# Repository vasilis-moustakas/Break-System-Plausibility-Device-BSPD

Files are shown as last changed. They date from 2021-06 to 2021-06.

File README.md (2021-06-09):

# Break System Plausibility Device (BSPD)
## Project Report
* Project Report is [Here](https://github.com/vasilis-moustakas/Break-System-Plausibility-Device-BSPD/blob/main/Brake_System_Plausibility_Device.pdf)
## Circuit Preview

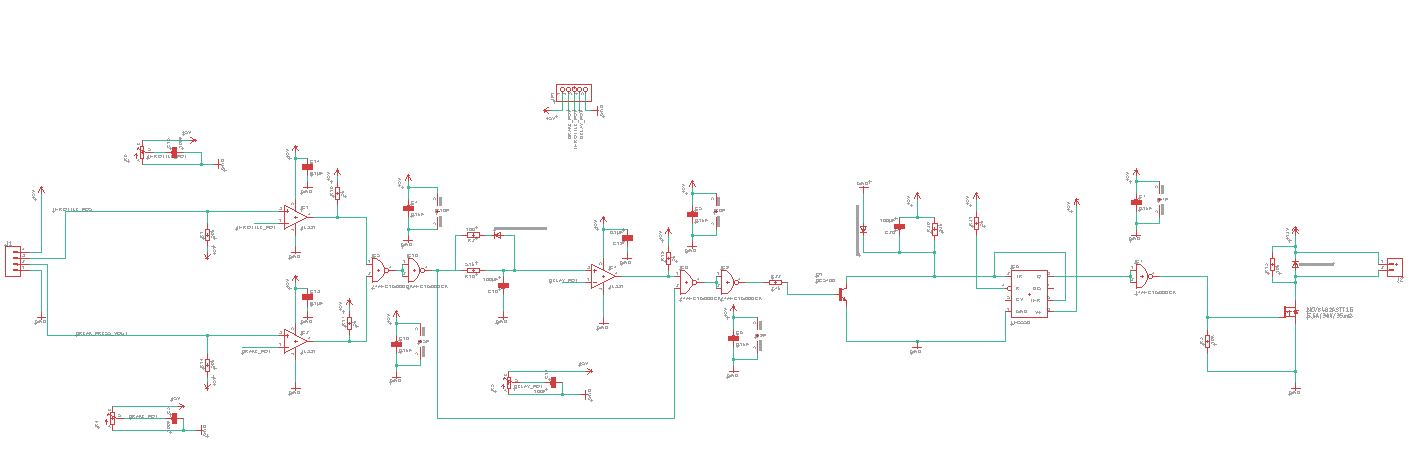
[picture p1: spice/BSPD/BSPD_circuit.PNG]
Circuit Preview


## PCB Preview
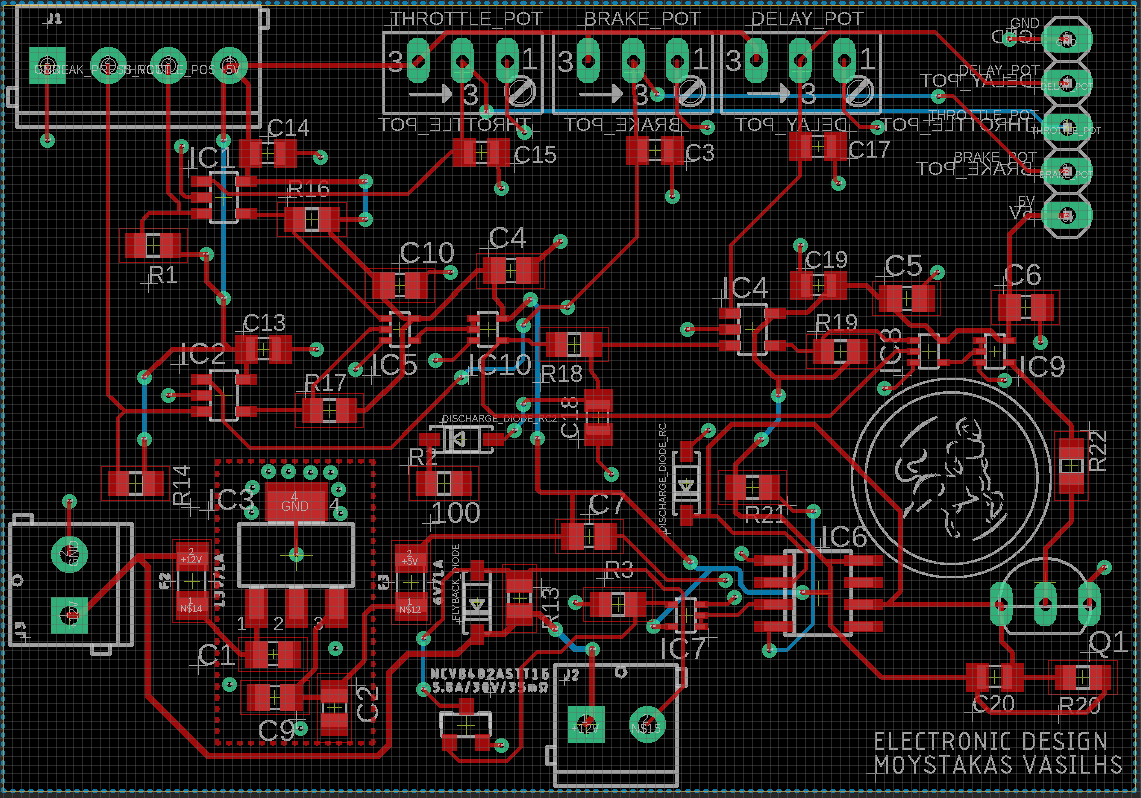
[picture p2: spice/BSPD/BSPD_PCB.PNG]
PCB Preview


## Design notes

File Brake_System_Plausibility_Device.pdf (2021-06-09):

# Brake System Plausibility Device

Vasileios Moustakas

February 2021

## 1 Introduction

With electronic throttle control systems becoming mandatory for FSAE competitions so are BSPDs . Brake System Plausibility Device (BSPD) is a standalone non-programmable circuit, witch must stop the current provision when hard braking occurs and the throttle position is more than 25 percent over the idle position for more than 500ms . Furthermore throttle and brake sensors must be able to be disconnected separately .

## 2 Regulator

As a circuit BSPD works with a 5 volts VDD but the cars battery provides 12 volts in order to reduce the voltage an LM340MP regulator was selected with 3 decoupling capacitors as shown in Fig. 1. Because the car battery is positioned away from the PCB, in case of a momentary high load there is a chance of a voltage drop due to the wiring. In that case the input capacitor of the regulator C1 provides the circuit the mandatory load for a small period of time. The regulators output capacitor improve stability, the time response of the regulator and filter part of the noise of the bandwidth. The values of the capacitors were selected according to the data sheet.

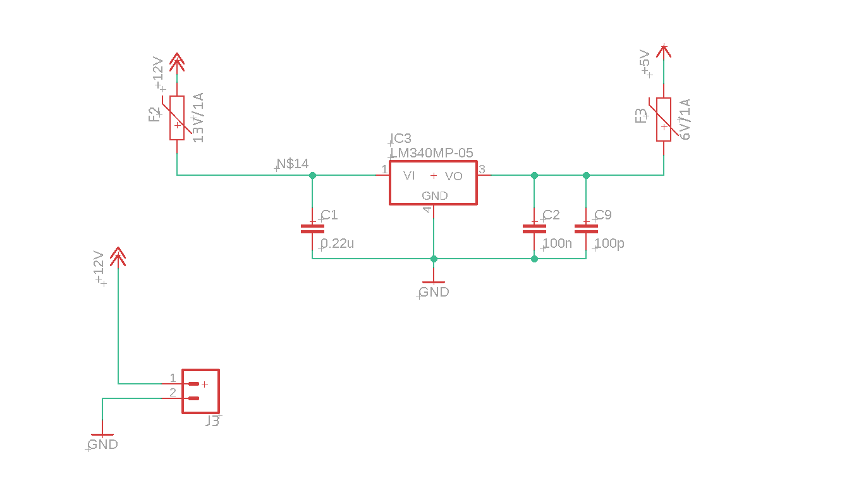
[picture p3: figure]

Figure 1: Regulator circuit

1

## 3 Comparisons and Implausibility Verification

In order to disconnect the sensor separately at any given time they must not be in the PCB and they are connected with it with a pin connector. In both sensor signal a 50K pull down resistance is connected thus when disconnecting the sensors the input signal will not be floating . The value of those resistances must be much higher of the sensor resistance in order not to interfere with the input signal. The signal from both sensor passes through an operational amplifier comparing the signals voltage with a threshold set by the user via a potentiometer in order do detect hard breaking and the throttle position. When the signal voltage is higher than the threshold op-amp is triggered providing 5 volts at the output. A 5K ohm pull up resistor is placed on output in case of an op-amp failure to provide 5V output. Both signals are connected with 2 nand gates (making an AND gate) to pass a high signal only if both throttle and brake signal are high. As set by the rules in order to trigger shut down both signal must be high for more than 500ms as such an rc filter with values 100uf for the capacitor and 5.1k(5.1 because nand gates are not ideal and the output wont be exactly 5 volts) for the resistor accompanied by an op-amp are connected with the set of nand gates . The rc filter has a time constant of 510ms given the equation for the capacitor’s charging :

Vc = Vin − (V ∗ exp (−t/(R ∗ C))) | (1)

we get an estimated 3.15 volts for the potentiometer on the other terminal of the op-amp. Finally if an implausibility happens for less than 500ms a diode is placed in order to discharge the capacitor. The capacitor is discharged to 0.7 through the diode and the 100ohm resistor and from 0.7 to 0 through the 5.1 kohm resistor. We can see all this in Fig .2

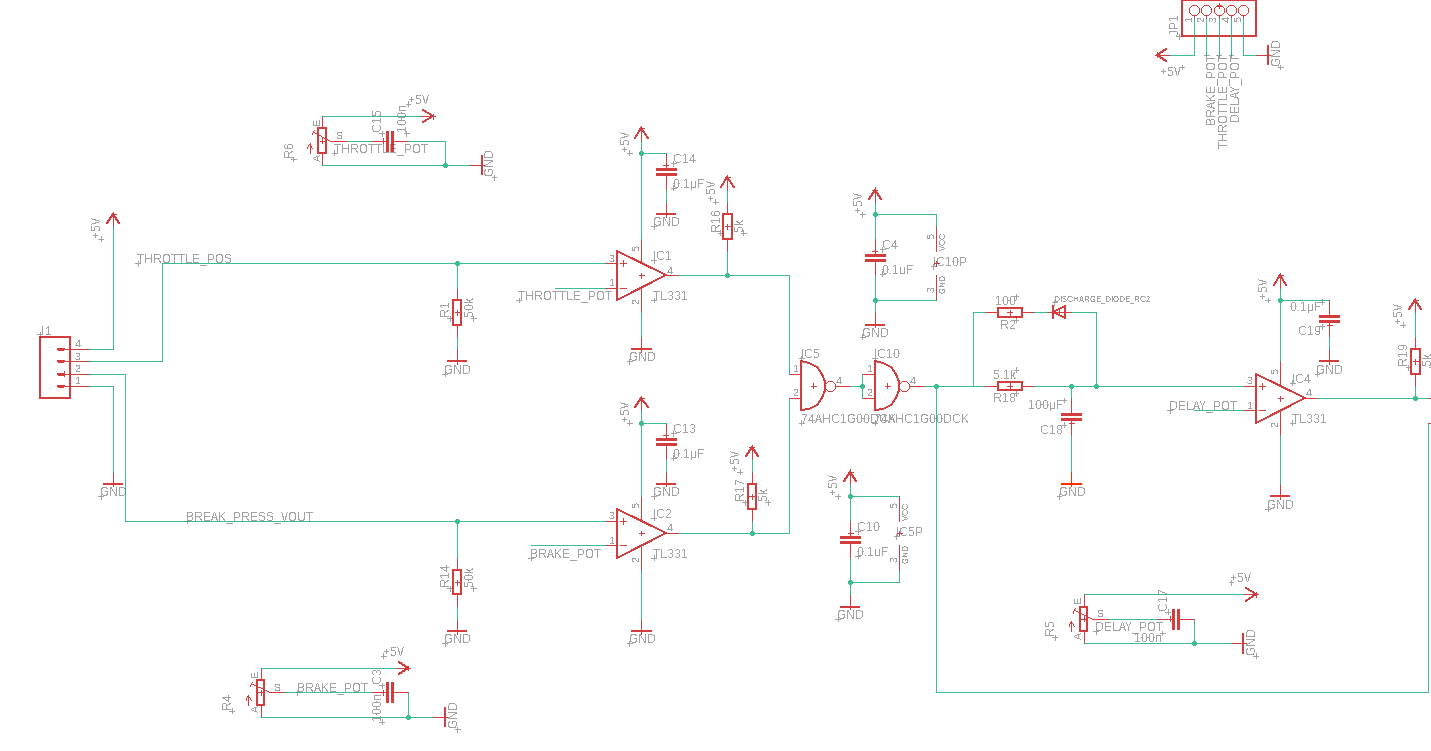
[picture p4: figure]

Figure 2: 1st part of the circuit

2

## 4 Reset Mechanisms

In order to understand the reset mechanisms first comprehend the working principle of the lm555. As shown in Fig .3 both trigger and threshold are sorted and the capacitor is connected directly to 5V so when the car powers up the capacitor instantly goes to 5V in order to avoid any false triggers. So when no implausibilities are present the bjt is open and the trigger threshold node is an open circuit, as a result its has a voltage of 5V . When VDD is present in both trigger and threshold the SR flip flop inside the lm555 goes high but the output driver inside the lm555 takes it back down to 0 so in order for the circuit to work correctly an inverter is placed on the output of the lm555. As we saw in the previous chapter when an implausibility is present for more than 500ms the bjt closes driving the trigger threshold node to GND thus the lm555 is now generating 0volts and the inverter drives it to 5volts. As stated by the rules the reset must trigger when the implausibility is aspsent for more than 10 seconds or when there is a power cycle. As for the power cycle rule when the car’s power is shut down the capacitor is immediately discharged by the diode thus reseting the lm555 output back to 0 volts. As for the 10 second rule the voltage on the trigger threshold node must reached 2/3 VDD in order to change the lm555 state thus a 100uF capacitor and a 92 kohm resistor were selected making for a timing constant of 9.2 seconds and 10 second delay for the capacitor to reach 2/3 VDD, using the equation: (1)

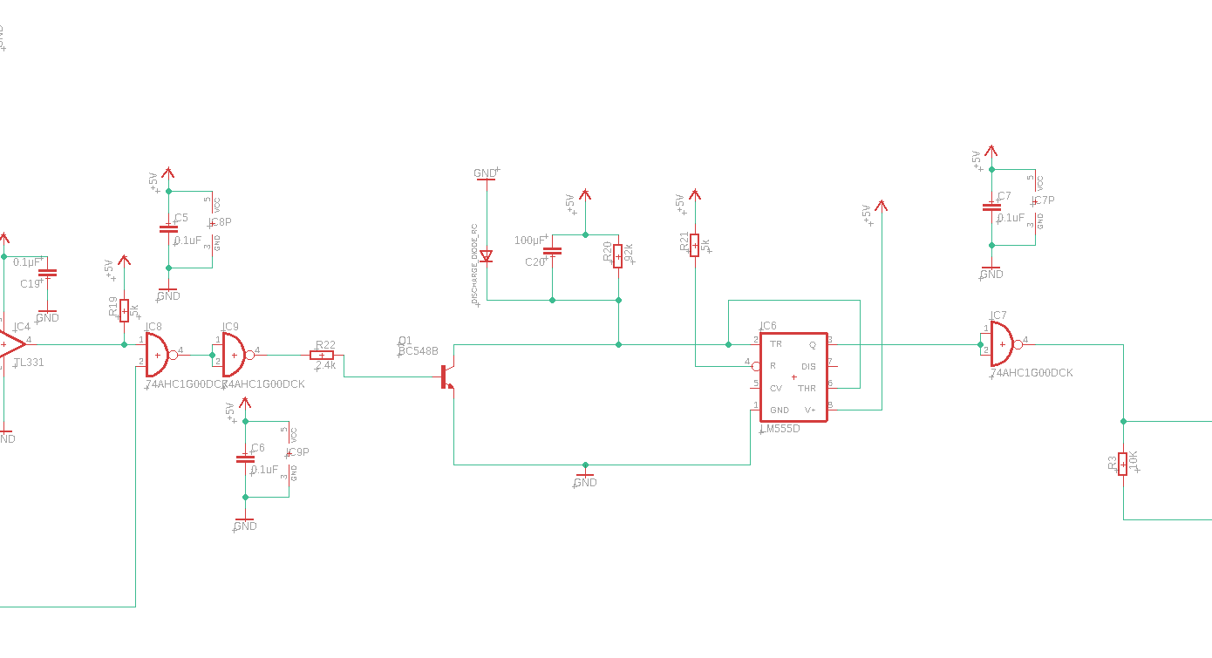
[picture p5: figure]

Figure 3: 2nd part of the circuit

3

## 5 Relay Trigeer

Finally when an implausibility is present the output of the the inverter is high thus closing the MOSFET and dragging the one terminal of the relay to 0 volts . As a results the voltage difference between the 2 terminals of the relay is 12 Volts triggering the shut down. When no implausibility is present both terminals stands at 12 volts thus not triggering the relay. Furthermore a flyback diode is placed in orded to avoid any spices due to the triggering of the coil inside the relay and a 10k pull down resistor is placed between the gate opf the MOSFET and the ground insuring that the gate can be discharged through that resistor as shown in Fig .3.

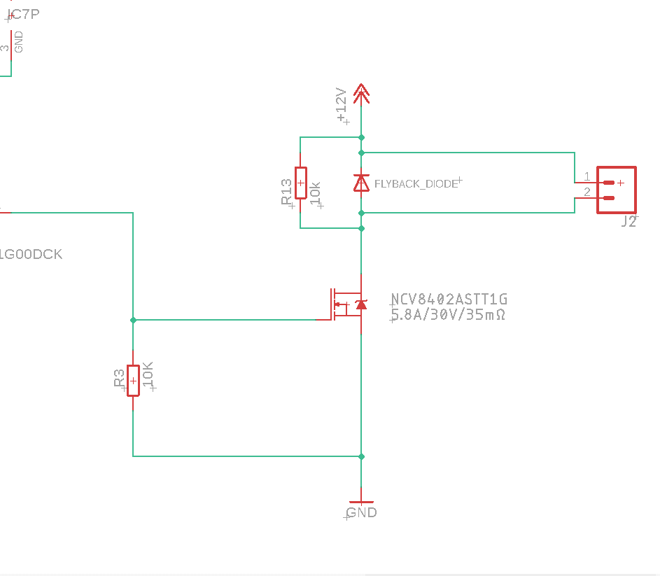
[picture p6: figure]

Figure 4: 3rd part of the circuit

4

## 6 Full circuit


Figure 5: Full circuit

## 7 Simulation results

The proposed circuit was designed using autodesk EAGLE and simulated with ltspice . As shown in Fig .6 when the implausbility lasts for 500ms or less there is no trigger of the relay and the capacitor is almost immediately discharged. When an 8 sec implausibility as present the relay stays always open as shown in Fig .7. Finally when analyzing a 10 second or longer implausibility or a power cycle reset occurs as shown in Fig .8 and Fig .9 working as demonstrated in the previous sections.

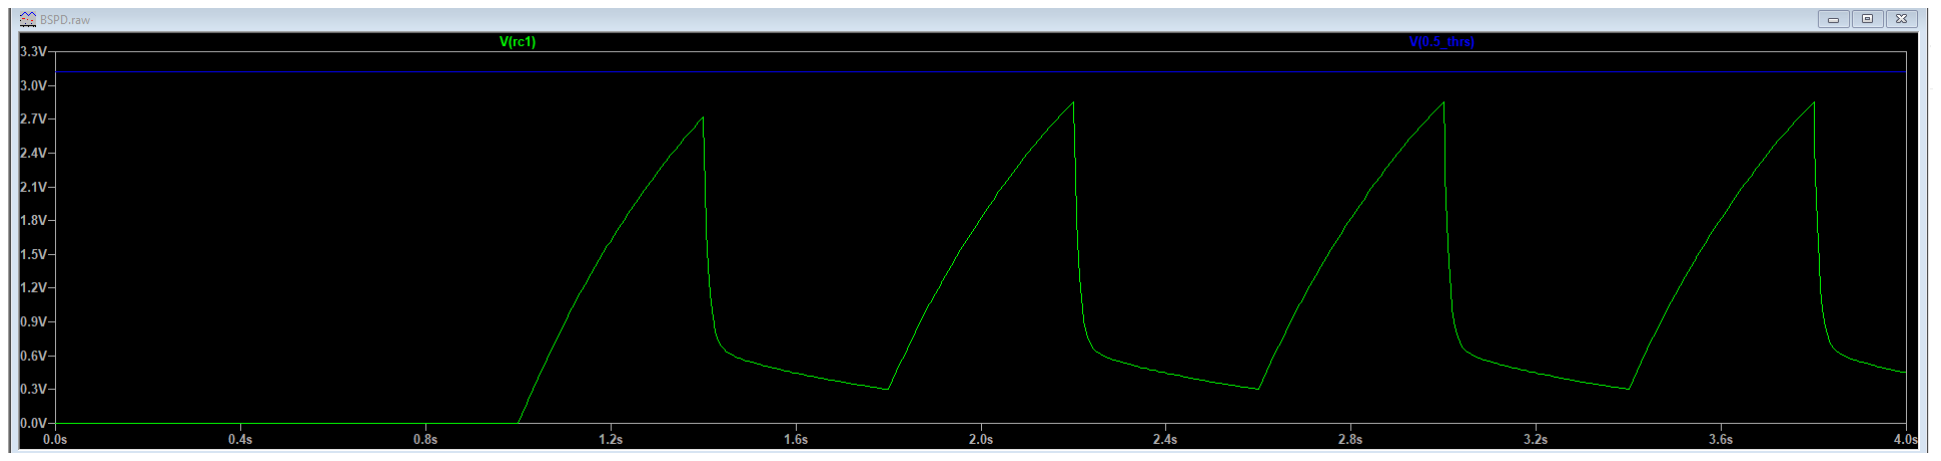
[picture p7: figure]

Figure 6: Full circuit

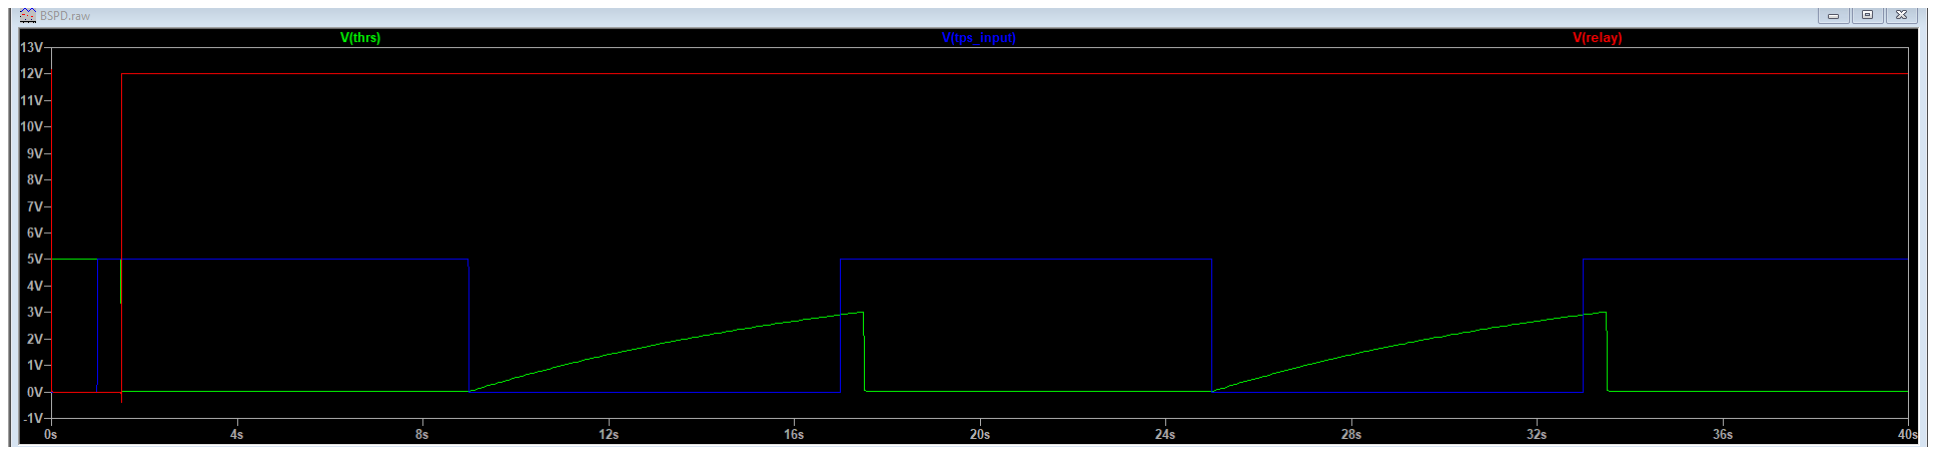
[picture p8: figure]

Figure 7: Full circuit

5

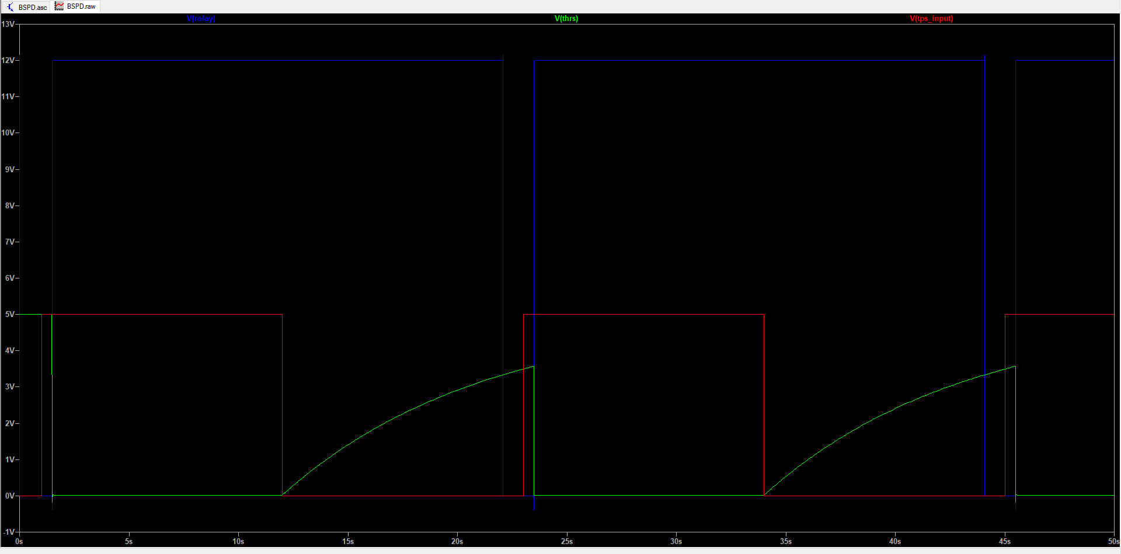
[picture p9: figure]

Figure 8: Full circuit

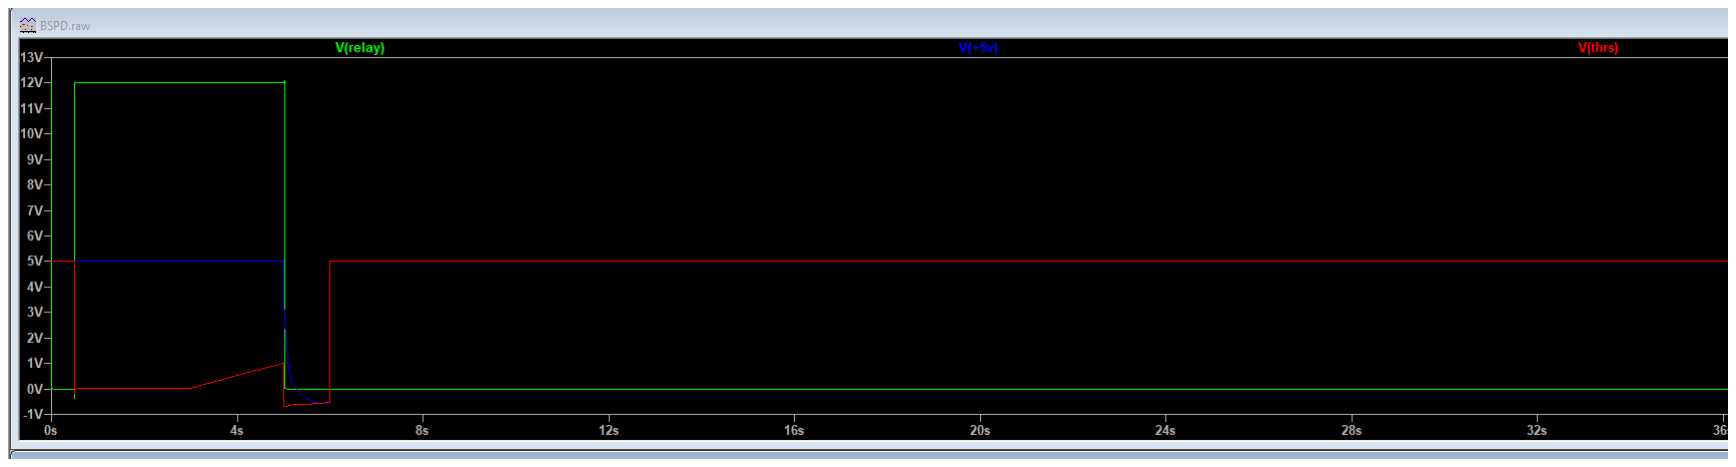
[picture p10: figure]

Figure 9: Full circuit

6

## 8 PCB

When designing the PCB decoupling components were placed as close as possible to their respective components so in case of voltage drop they could instantly provide the necessary voltage to those components. The PCB is a layer design with vias to connect them and when 2 traces are crossing each other they do it in a 90 degree angle in order to avoid electromagnetic interferences. As much of the interconnects as possible were placed on the top layer. This is where the pins of the parts are already anyway, so is the logical layer to use to connect them. Then bottom plane is used for short ”jumpers” only when needed to make the routing work. The bottom plane is otherwise ground. Further more in order to reduce to resistance in power lines their width is higher so the efficiency becomes greater . Finally to reduce the EMI crossing between top and bottom layer traces happens in a 90 degree angle so the interference is minimized and a top group plane was added this means there is no need for a separate via for the ground side of the bypass cap. As a result power loop connects directly to the ground pin on the top side, then net is connected to the ground plane with a via at a single point.

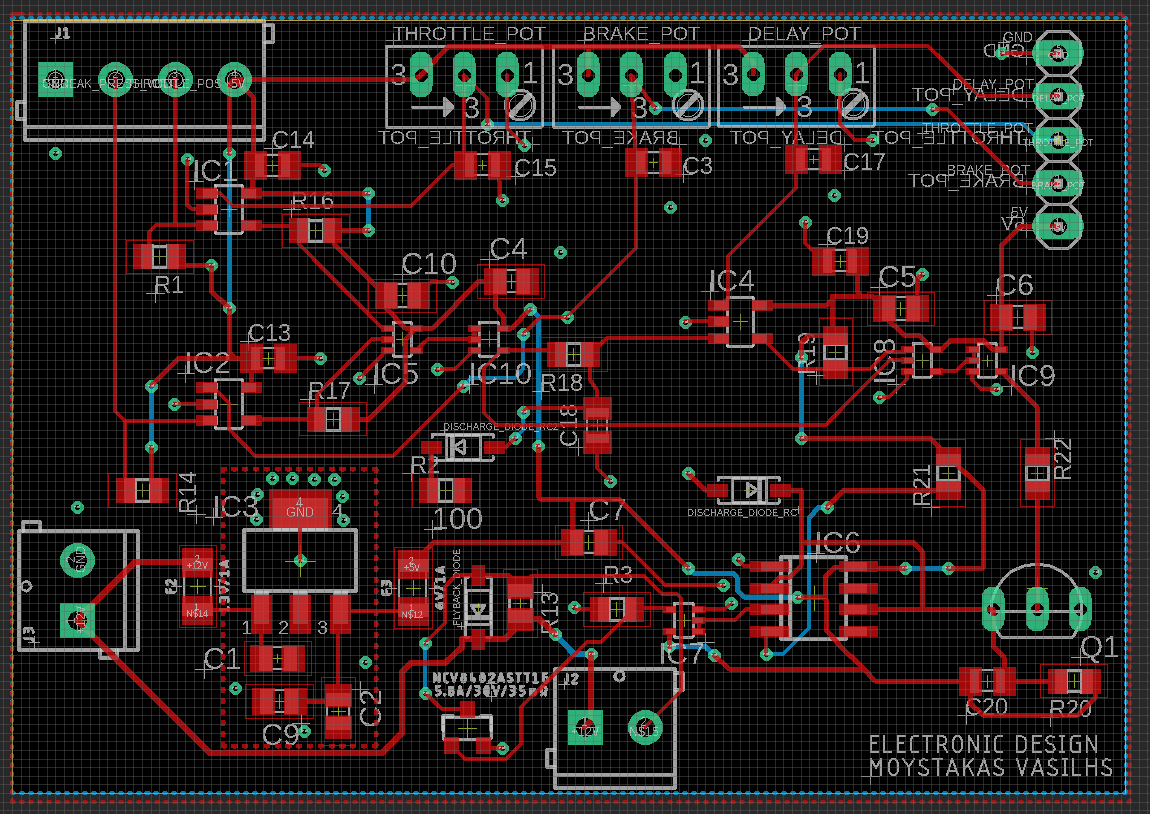
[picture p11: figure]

Figure 10: PCB

7

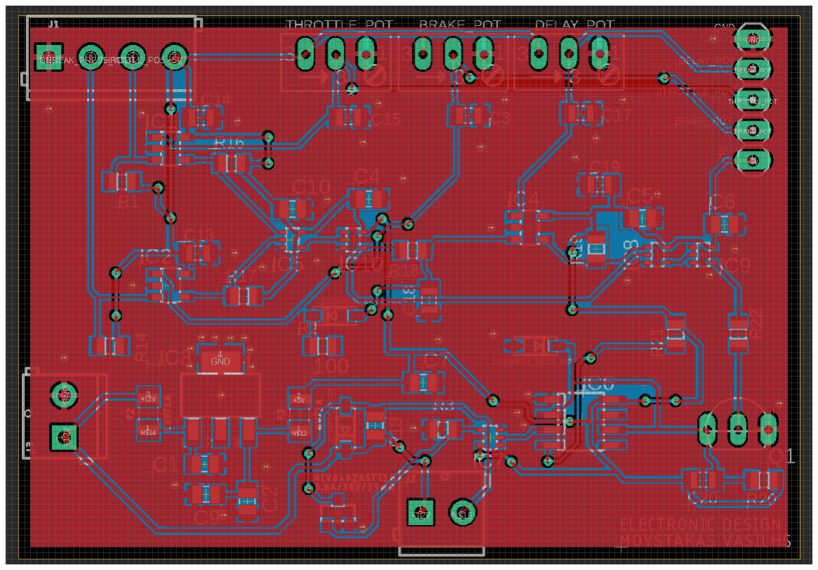
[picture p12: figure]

Figure 11: PCB with ground planes

8

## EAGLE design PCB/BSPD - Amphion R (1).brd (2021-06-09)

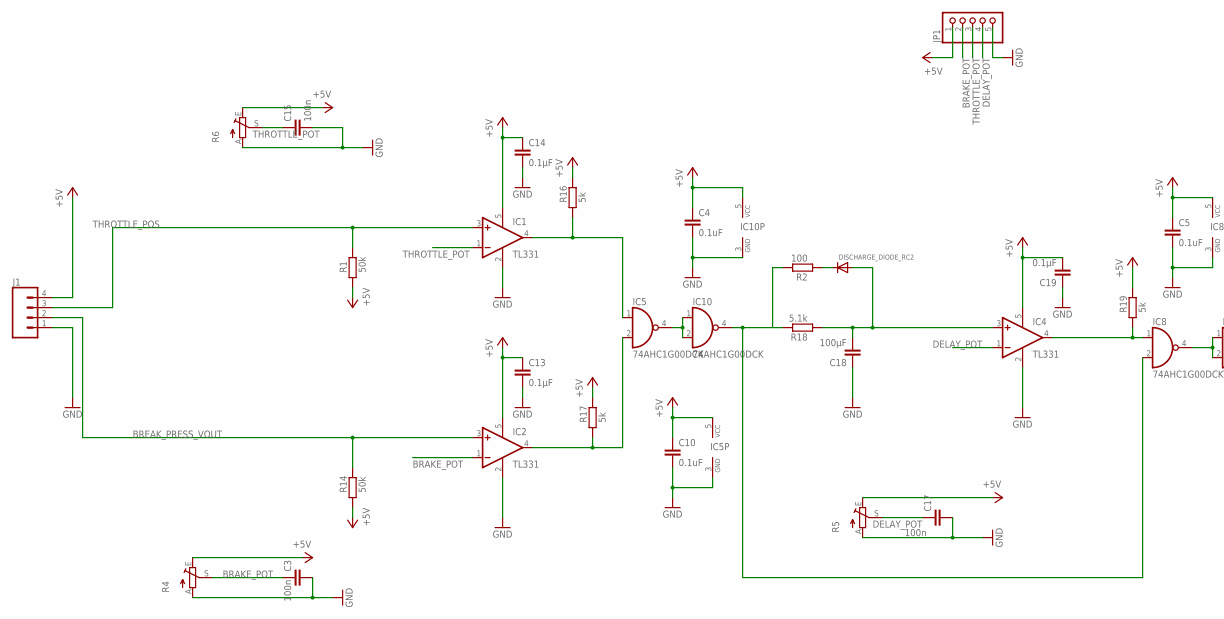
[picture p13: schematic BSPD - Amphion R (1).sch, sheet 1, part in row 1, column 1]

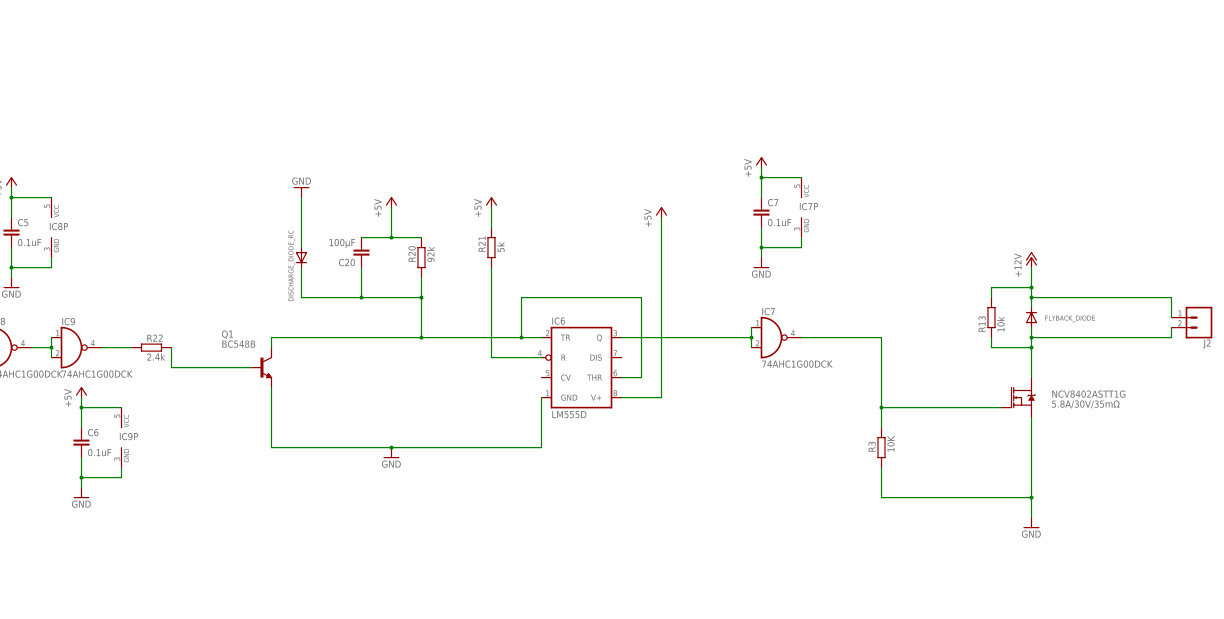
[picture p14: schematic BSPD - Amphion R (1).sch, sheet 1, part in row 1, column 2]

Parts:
C3, C15, C17: 100n; C0805K
C4, C5, C6, C7, C10: 0.1uF; C0805
C13, C14, C19: 0.1μF; C0805K
C18, C20: 100μF; C0805K
DISCHARGE_DIODE_RC, DISCHARGE_DIODE_RC2: DIODESOD-123; SOD-123
FLYBACK_DIODE: DIODESOD-123; SOD-123
IC1, IC2, IC4: TL331; DBV-R-PDSO-G5
IC5, IC7, IC8, IC9, IC10: 74AHC1G00DCK; SC70-5
IC6: LM555D; SO08
J1: CONN_04SCREW; SCREWTERMINAL-3.5MM-4
J2: CONN_023.5MM; SCREWTERMINAL-3.5MM-2
JP1: PINHD-1X5; 1X05
NCV8402ASTT1G: 5.8A/30V/35mΩ; SOT23-3
Q1: BC548B; TO92-EBC
R1, R14: 50k; R0805
R2: 100; R0805
R3: 10K; R0805
R4, R5, R6: TRIM_EU-RJ9W; RJ9W
R13: 10k; R0805
R16, R17, R19, R21: 5k; R0805
R18: 5.1k; R0805
R20: 92k; R0805
R22: 2.4k; R0805

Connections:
+5V: C4.1, C5.1, C6.1, C7.1, C10.1, C13.1, C14.1, C19.2, C20.2, IC1.5 (V+), IC2.5 (V+), IC4.5 (V+), IC5.5 (VCC), IC6.8 (V+), IC7.5 (VCC), IC8.5 (VCC), IC9.5 (VCC), IC10.5 (VCC), J1.4, JP1.1, R1.1, R4.E, R5.E, R6.E, R14.1, R16.2, R17.2, R19.2, R20.2, R21.2; also elsewhere on the board
+12V: FLYBACK_DIODE.C, J2.1, R13.2; also elsewhere on the board
AND_VOLTAGE: IC8.2 (I1), IC10.4 (O), R18.2
BRAKE_POT: C3.1, IC2.1 (-IN), JP1.2, R4.S
BREAK_PRESS_VOUT: IC2.3 (+IN), J1.2, R14.2
DELAY_POT: C17.1, IC4.1 (-IN), JP1.4, R5.S
GND: C3.2, C4.2, C5.2, C6.2, C7.2, C10.2, C13.2, C14.2, C15.2, C17.2, C18.1, C19.1, DISCHARGE_DIODE_RC.A, IC1.2 (GND), IC2.2 (GND), IC4.2 (GND), IC5.3 (GND), IC6.1 (GND), IC7.3 (GND), IC8.3 (GND), IC9.3 (GND), IC10.3 (GND), J1.1, JP1.5, NCV8402ASTT1G.2 (S), Q1.E, R3.1, R4.A, R5.A, R6.A; also elsewhere on the board
GND2: C18.2, DISCHARGE_DIODE_RC2.A, IC4.3 (+IN), R18.1
unnamed: IC1.4 (OUT), IC5.1 (I0), R16.1
unnamed: IC2.4 (OUT), IC5.2 (I1), R17.1
unnamed: IC4.4 (OUT), IC8.1 (I0), R19.1
unnamed: DISCHARGE_DIODE_RC2.C, R2.1
unnamed: IC5.4 (O), IC10.1 (I0), IC10.2 (I1)
unnamed: IC9.4 (O), R22.1
unnamed: Q1.B, R22.2
unnamed: IC6.4 (R), R21.1
unnamed: C20.1, DISCHARGE_DIODE_RC.C, IC6.2 (TR), IC6.6 (THR), Q1.C, R20.1
unnamed: IC6.3 (Q), IC7.1 (I0), IC7.2 (I1)
unnamed: IC7.4 (O), NCV8402ASTT1G.1 (G), R3.2
unnamed: IC8.4 (O), IC9.1 (I0), IC9.2 (I1)
unnamed: FLYBACK_DIODE.A, J2.2, NCV8402ASTT1G.3 (D), R13.1
THROTTLE_POS: IC1.3 (+IN), J1.3, R1.2
THROTTLE_POT: C15.1, IC1.1 (-IN), JP1.3, R6.S

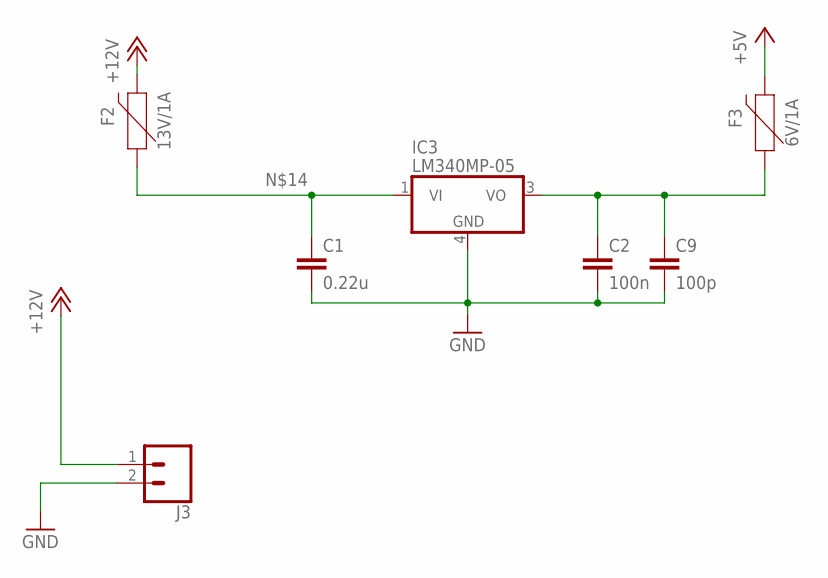
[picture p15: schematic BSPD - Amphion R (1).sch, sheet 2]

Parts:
C1: 0.22u; C0805
C2: 100n; C0805
C9: 100p; C0805
F2: 13V/1A; 1206
F3: 6V/1A; 1206
IC3: LM340MP-05; SOT223
J3: CONN_023.5MM; SCREWTERMINAL-3.5MM-2

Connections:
+5V: F3.2; also elsewhere on the board
+12V: F2.2, J3.1; also elsewhere on the board
GND: C1.2, C2.2, C9.2, IC3.4 (GND), J3.2; also elsewhere on the board
unnamed: C2.1, C9.1, F3.1, IC3.3 (VO)
unnamed: C1.1, F2.1, IC3.1 (VI)

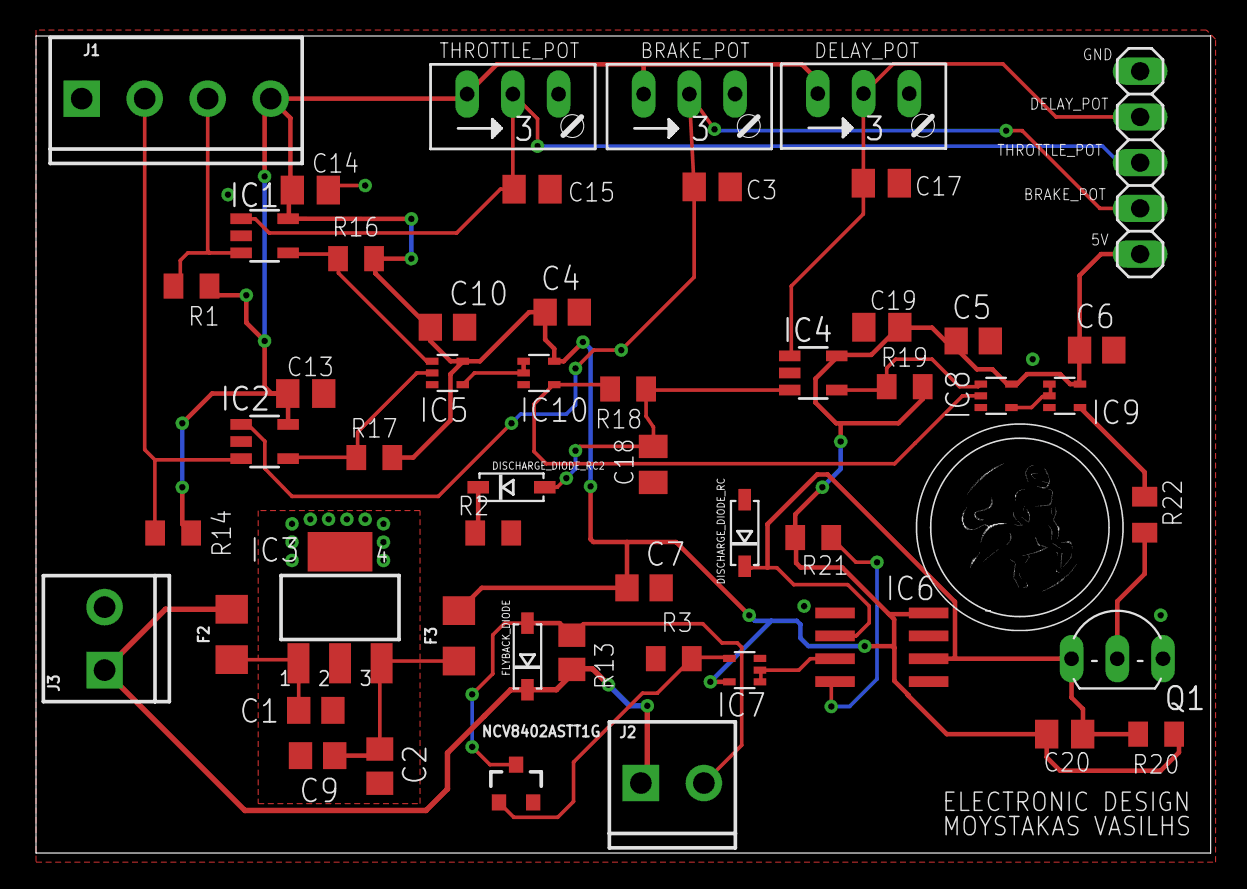
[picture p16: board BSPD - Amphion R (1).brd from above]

Board: 2 copper layers, 65.3 x 45.4 mm, 52 parts (0 on the bottom side), 25 nets.

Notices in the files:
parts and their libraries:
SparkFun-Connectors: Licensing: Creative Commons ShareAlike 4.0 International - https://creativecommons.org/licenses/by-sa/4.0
